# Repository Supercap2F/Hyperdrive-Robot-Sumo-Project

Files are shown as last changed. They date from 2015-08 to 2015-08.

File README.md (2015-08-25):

# Hyperdrive-Robot-Sumo-Project
Open Source Robot Sumo Project

* Start Date: Friday, November 28, 2014
*  End Date: ---
*   Version: 1.0

# About
The project started out on November 28th, 2014 - But under a different name: "Epsilon - The Universal Robot".
After more work was done, it was changed to "Hyperdrive!", named after my one of my favorite songs from the band
Guardian. The robot's main function is for Robot sumo, but will also have programs that will allow it to also
be a line flowing robot, and more.

#### Note: You can find photos of the robot in: Hyperdrive-Robot-Sumo-Project/Images/Robot Photos

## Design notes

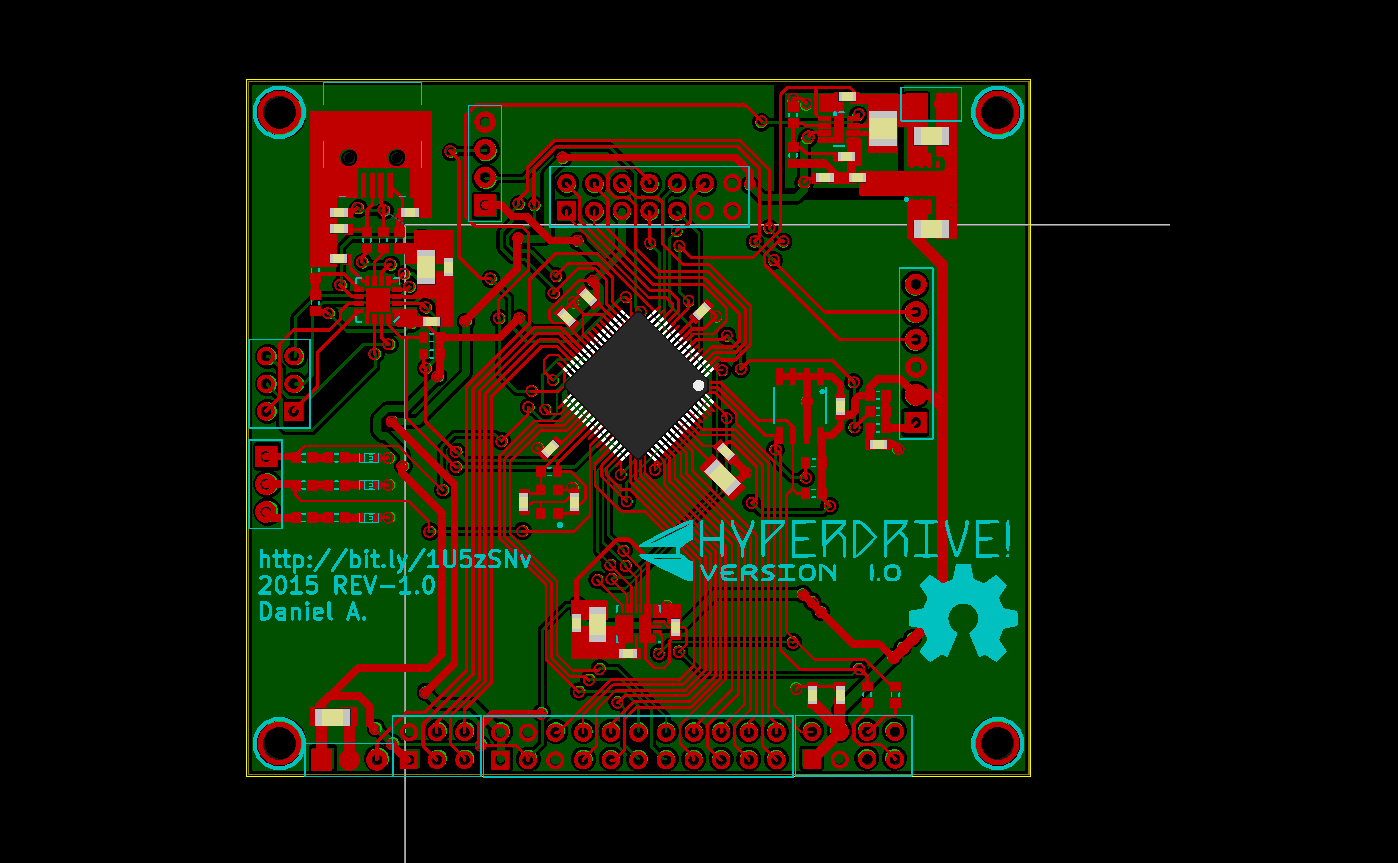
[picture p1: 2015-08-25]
Images/Robot Photos/Hyperdrive_Main_PCB.png

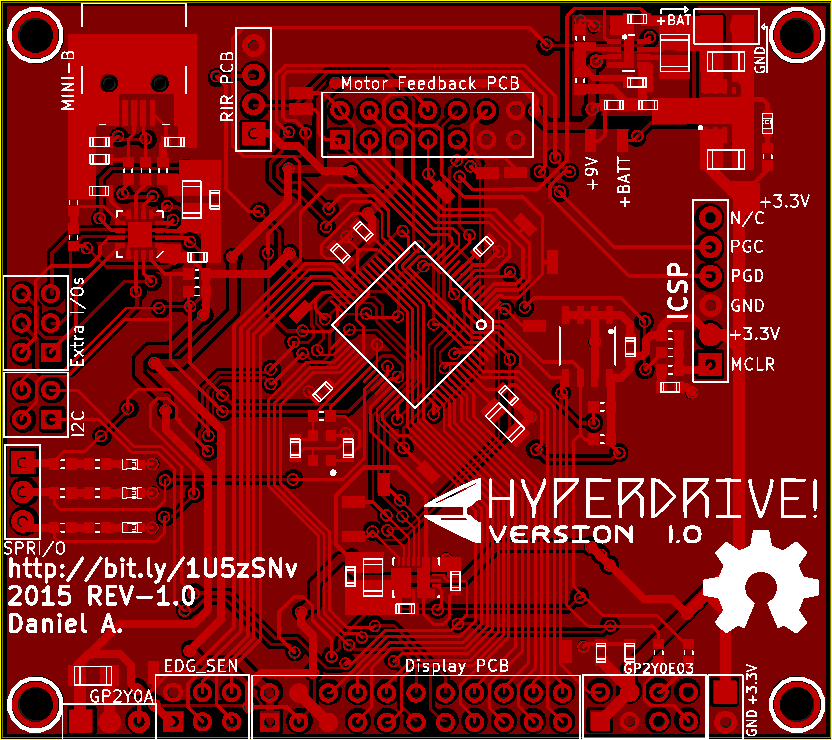
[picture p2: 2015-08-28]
Images/Robot Photos/Hyperdrive_Main_PCB#2.JPG

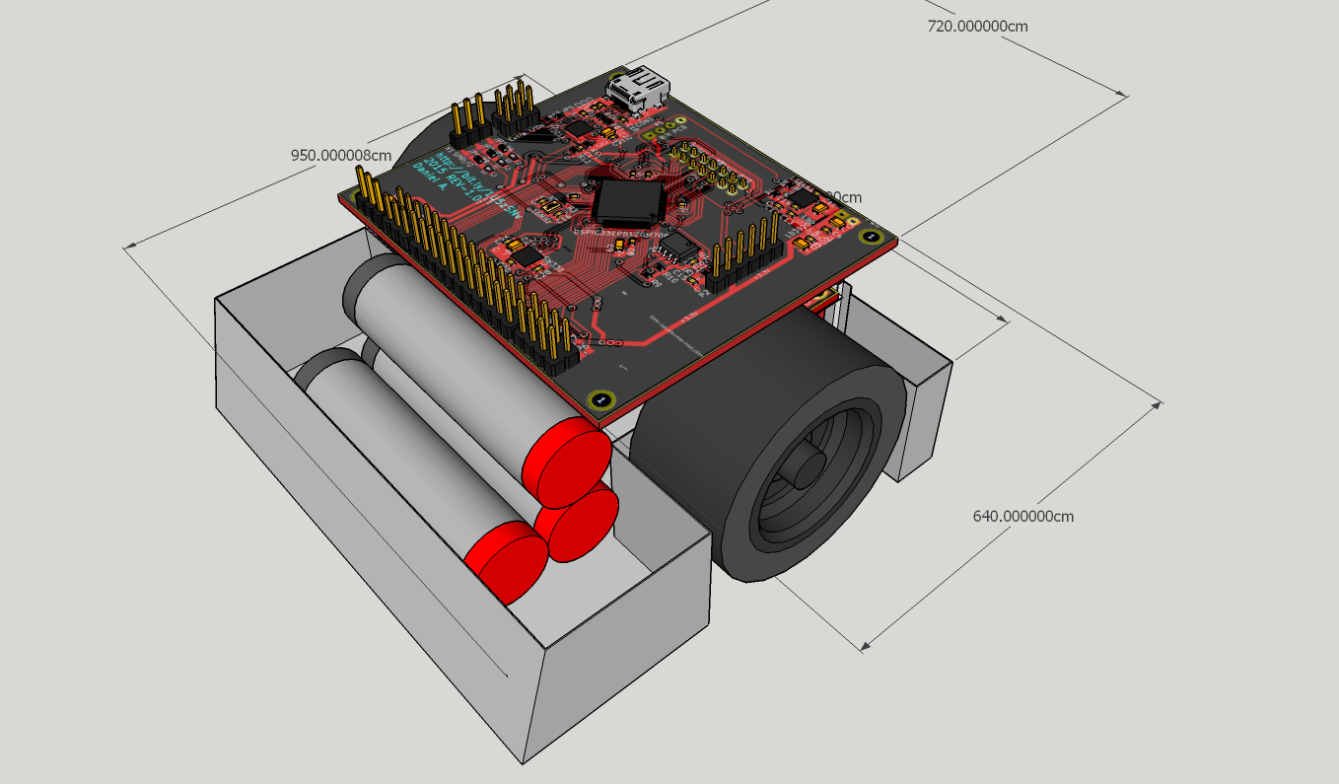
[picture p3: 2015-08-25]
Images/Robot Photos/Hyperdrive_3D_Model_#1.png

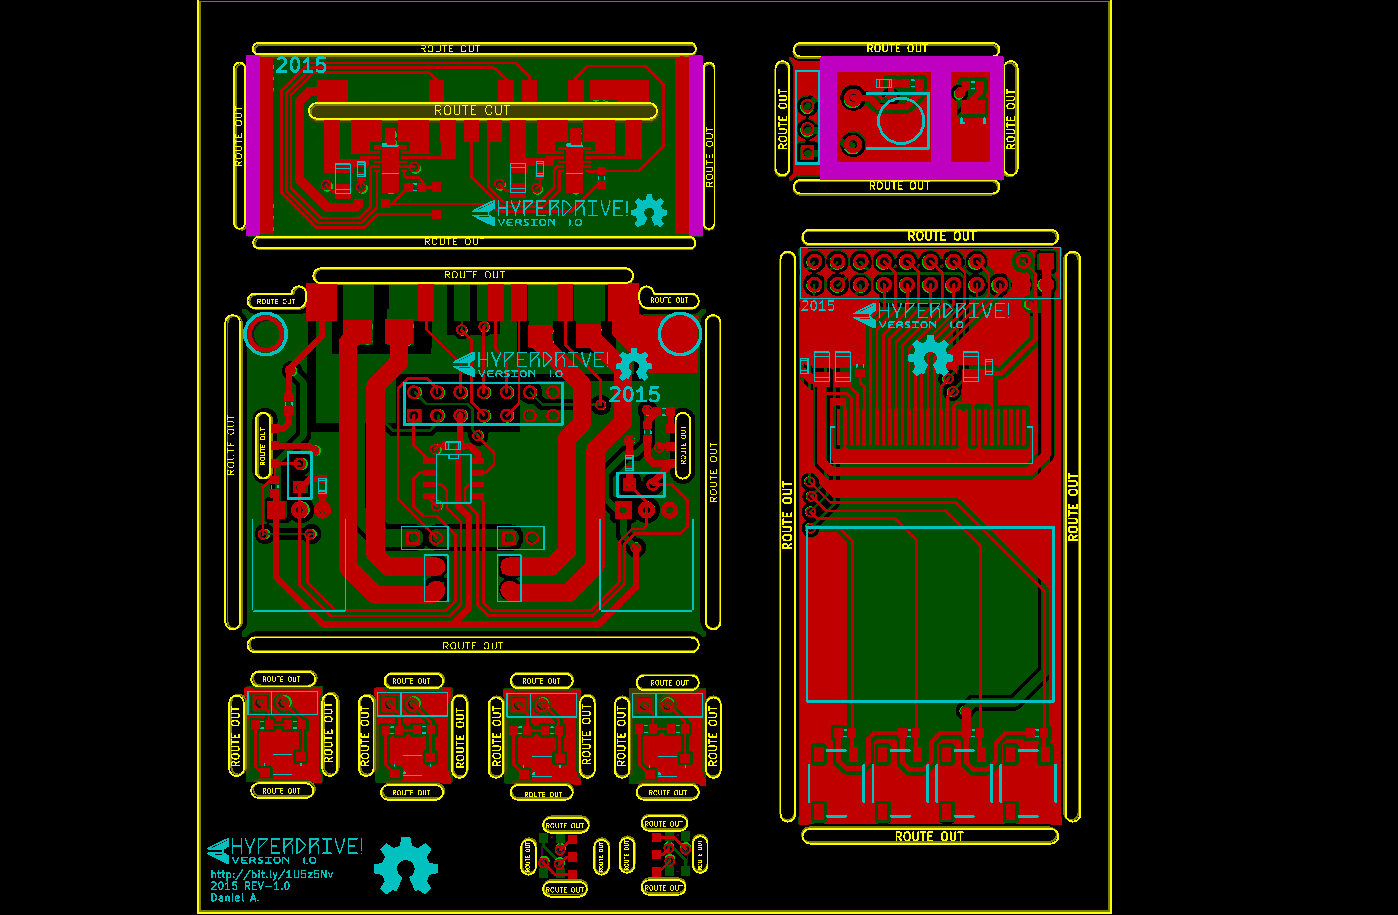
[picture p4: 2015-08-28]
Images/Robot Photos/Hyperdrive!_Odd_PCB_Photo.png

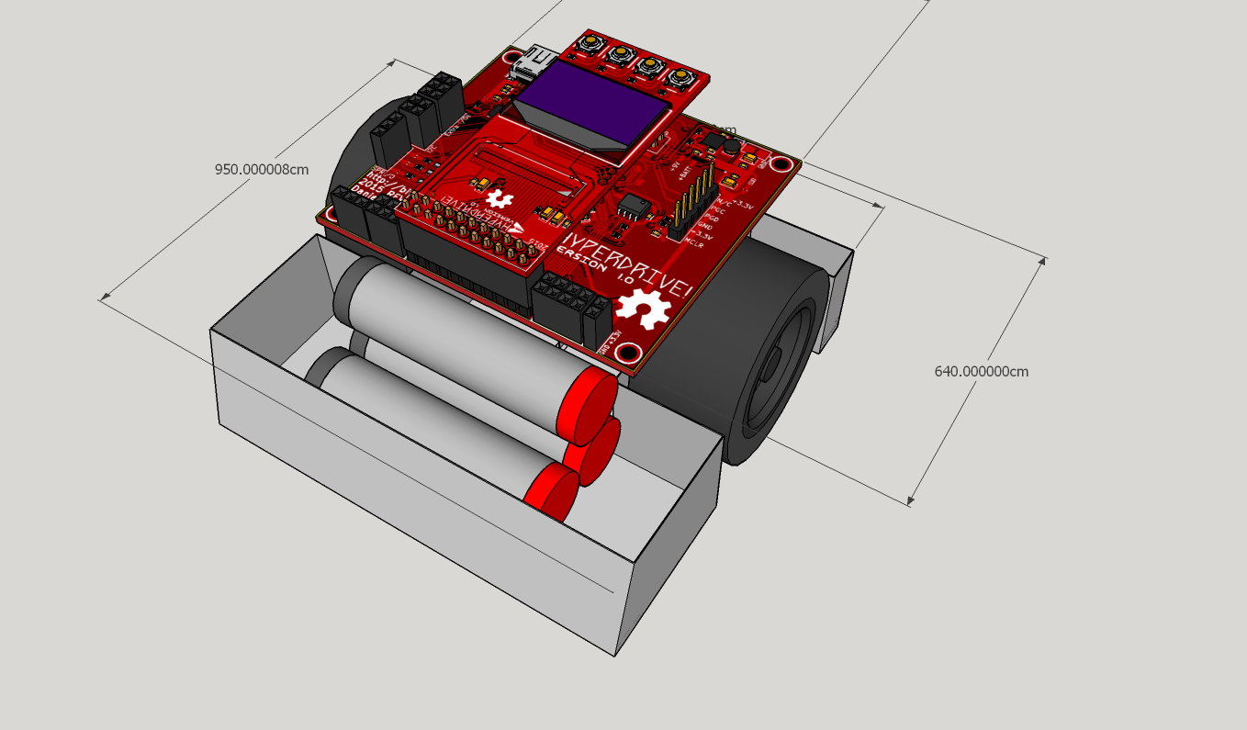
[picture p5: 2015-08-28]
Images/Robot Photos/Hyperdrive_3D_Model_#3.png

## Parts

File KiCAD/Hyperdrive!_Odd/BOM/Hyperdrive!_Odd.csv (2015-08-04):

ref | value | footprint | Type | Price | Digikey Part No.
C1 | 10u | ~ | Tan
C2 | 1u | ~ | Ceramic
C3 | 10u | ~ | Tan
C4 | 1u | ~ | Ceramic
C5 | 0.1u | ~
C6 | 100n | ~
C7 | 100n | ~
C8 | 100n | ~
C9 | 2.2u | ~
C10 | 4.7u | ~
C11 | 2.2u | ~
C12 | 100n | ~
K1 | ES1
K2 | ES2
K3 | ES3
K4 | ES4
LCD1 | 128X64_LCD | ~
P1 | CONN_16
P2 | H-Bridge PCB
P3 | Main Processor PCB
P4 | MR
P5 | ML
P6 | CONN_22 | ~
R1 | 10K | ~
R2 | 160 | ~
R3 | 10K | ~
R4 | 160 | ~
R5 | 10K | ~
R6 | 160 | ~
R7 | 10K | ~
R8 | 160 | ~
R9 | 10K | ~
R10 | 10K | ~
R11 | 160 | ~
R12 | 10K | ~
R13 | 160 | ~
R14 | 10K | ~
R15 | 10K | ~
R16 | 10K | ~
R17 | 10K | ~
R18 | 10K | ~
R19 | 560K | ~
RV1 | 50K | ~
RV2 | 50K | ~
SW1 | SW_PUSH | ~
SW2 | SW_PUSH | ~
SW3 | SW_PUSH | ~
SW4 | SW_PUSH | ~
U1 | MAX14780
U2 | QRE1113 | ~
U3 | QRE1113 | ~
U4 | MAX14780
U5 | QRE1113 | ~
U6 | QRE1113 | ~
U7 | MCP6541 | ~
U8 | QRE1113 | ~
U9 | QRE1113 | ~

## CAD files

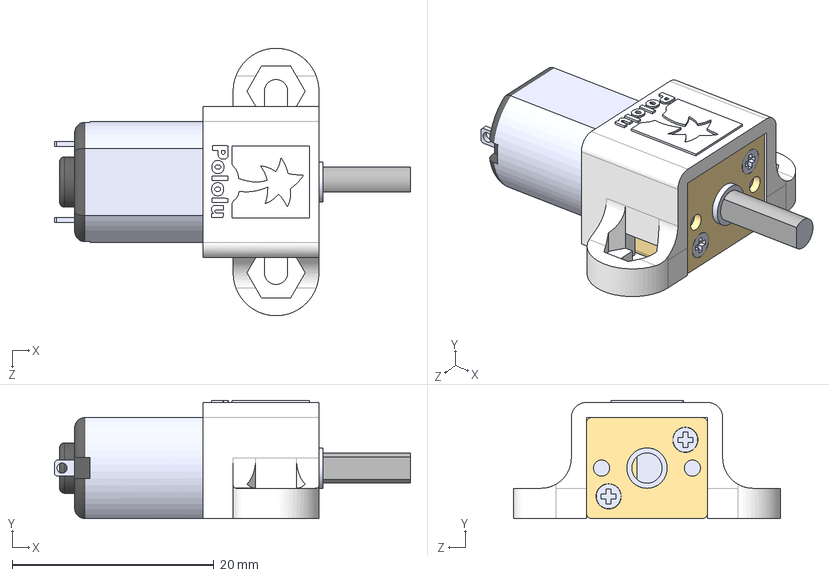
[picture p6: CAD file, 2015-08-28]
3D-Models/Components/micro-metal-gearmotor-with-1086-bracket.step
35.3 x 11.7 x 26.5 mm

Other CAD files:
3D-Models/Components/1200mAh_LiPoly.skp
3D-Models/Components/43.2x22_Wheel.skp
3D-Models/Components/Display.skp
3D-Models/Components/Display_PCB.skp
3D-Models/Components/Gull_Wing.skp
3D-Models/Components/Header_11x2.skp
3D-Models/Components/Header_2x1.skp
3D-Models/Components/Header_2x2.skp
3D-Models/Components/Header_3x1.skp
3D-Models/Components/Header_3x2.skp
3D-Models/Components/Header_4x2.skp
3D-Models/Components/Header_7x2.skp
3D-Models/Components/RB-POL-61-100x.skp

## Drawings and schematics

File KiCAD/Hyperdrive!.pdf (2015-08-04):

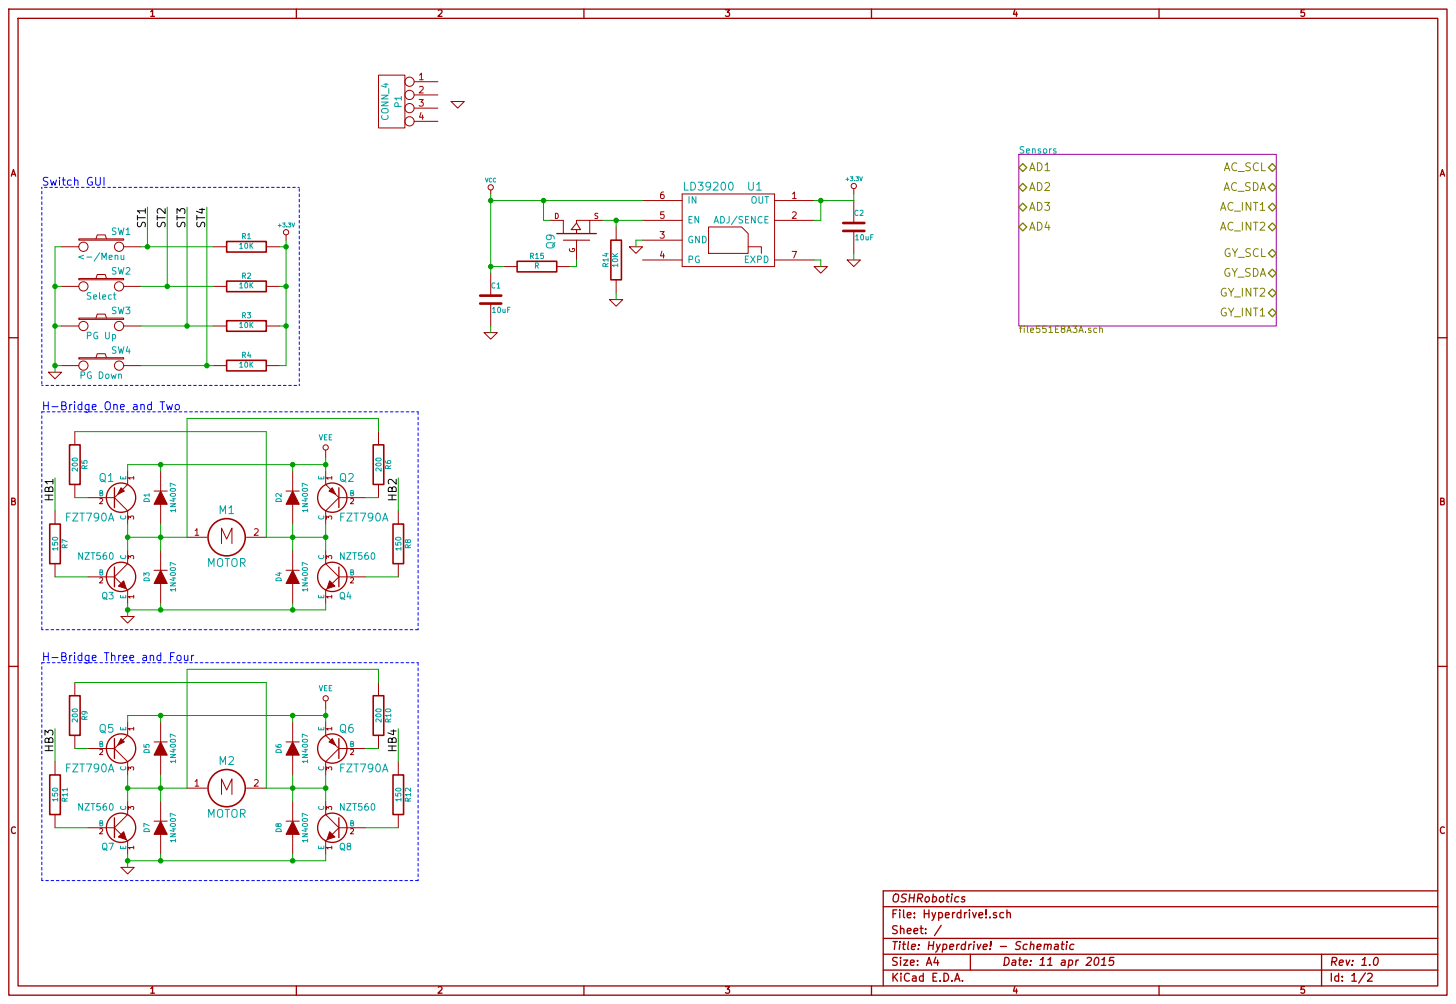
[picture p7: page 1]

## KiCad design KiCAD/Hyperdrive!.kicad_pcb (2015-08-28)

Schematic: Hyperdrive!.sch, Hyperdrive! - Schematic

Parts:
C1, C2, C6, C7, C8: 0.1u; Voltage 10-20V
C3, C4: 10uF
C5, C17, C18, C21, C23: 100n
C9: 10u; Voltage 16
C10, C14, C16: 20p
C11: 1u
C12: 0.47u
C13: 2.2u
C15: 0.1u
C19, C20: 47p
C22: 4.7u
CON1: USB-MINI-B
D1, D2, D3, D4: LED
FB1: 600R/1.3A
JP1: MCLR
JP2, JP3, JP4: JUMPER
JP5: RESET
K1: SPRI/O
L1: 47u
P1: RIR PCB
P2: ICSP
P3: Display PCB
P4: Motor Feedback PCB
P5: Extra I/Os
P7, P9: PWR
P8: I2C
R1, R13: 10K
R2: 100
R3: 1M
R4: 1908K
R5: 300K
R6, R7, R8: 220
R9, R10, R11, R12, R16: R
R14, R15: 27
TP1, TP2, TP3, TP4, TP5, TP6, TP7, TP8, TP9, TP10, TP11: TP
U1: 24AA256
U2: LD39200
U3: LT3464
U4: DSPIC33EP512GM706
U5: FT201X
X1: 16MHz

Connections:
+3.3V: C1.2, C2.1, C3.1, C5.1, C6.2, C7.1, C8.1, C17.1, P1.1, P2.2, P3.3, P4.5, P9.1, R1.2, R9.1, R10.1, R11.1, R12.1, R13.1, R16.1, TP2.1, U1.8 (Vcc), U2.1 (OUT), U2.2 (OUT), U2.3 (ADJ/SENCE), U4.10 (VDD), U4.19 (AVDD), U4.26 (VDD), U4.38 (VDD), U4.57 (VDD), U5.1 (VCCIO); also elsewhere on the board
+9V: C12.1, P3.1, P3.2, TP3.1, U3.3 (OUT)
+BATT: C4.1, C11.1, L1.2, P7.1, TP1.1, U2.6 (EN), U2.7 (IN), U2.8 (IN), U3.1 (CTRL), U3.7 (Vin), U4.12 (AN9/RPI27/RA11)
/CS#: P3.17, U4.52 (RP56/PWM5H/PMWR/RC8)
/D0: P3.9, U4.21 (OA3OUT/AN6/C3IN4-/C4IN1+/RP48/OCFB/RC0)
/D1: P3.10, U4.22 (OA3IN-/AN7/C3IN1-/C4IN1-/RP49/RC1)
/D2: P3.11, U4.23 (OA3IN+/AN8/C3IN3-/C3IN1+/RPI50/U1RTS/BC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)
/D3: P3.12, U4.35 (AN29/SCK1/RPI51/RC3)
/D4: P3.13, U4.36 (AN30/SDA1/RPI52/RC4)
/D5: P3.14, U4.37 (AN31/SCL1/RPI53/RC5)
/D6: P3.15, U4.50 (RP54/PWM6H/RC6)
/D7: P3.16, U4.51 (RP55/PWM6L/PMBE/RC7)
/D/C#: P3.6, U4.45 (AN48/CVREF2O/RPI58/PMCS1/RC10)
/DIRL: P4.7, TP7.1, U4.48 (TCK/AN26/CVREF1O/SOSCO/RP40/T4CK/RB8)
/DIRR: P4.10, TP10.1, U4.46 (OA5OUT/AN25/C5IN4-/RP39/INT0/RB7)
/E/RD#: P3.8, U4.47 (SOSCI/RPI61/RC13)
/FAULTL: P4.12, TP11.1, U4.60 (RP42/PWM3H/PMD0/RB10)
/FAULTR: P4.9, TP9.1, U4.49 (TMS/OA5IN-/AN27/C5IN4-/RP41/RB9)
/I/O1: JP2.2, K1.1, U4.11 (AN10/RPI28/RA12)
/I/O2: JP3.2, K1.2 (PM), U4.42 (RPI72/RD8)
/IRBDS: P1.2, U4.63 (RPI45/PWM2L/CTPLS/PMD3/RB13)
/IRPWM: P1.3, U4.62 (RPI44/PWM2H/PMD2/RB12)
/MCLR: JP1.2, P2.1, R1.1, R2.1
/MSL: P4.1, TP4.1, U4.14 (OA2IN+/AN1/C2IN1+/RPI17/RA1)
/MSR: P4.2, TP5.1, U4.13 (OA2OUT/AN0/C2IN4-/C4IN3-/RPI16/RA0)
/PGC: P2.5, U4.17 (PGEC1/OA1IN+/AN4/C1IN3-/C1IN1+/C2IN3-/R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)
/PGD: P2.4, U4.18 (PGED1/OA1IN-/AN5/C1IN1-/(CTMUC)/RP35/RT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)
/PWML: P4.8, TP8.1, U4.3 (RPI47/PWM1L/T5CK/T6CK/PMD7/RB15)
/PWMR: P4.6, TP6.1, U4.2 (RPI46/PWM1H/T3CK/T7CK/PMD6/RB14)
/R/W#: P3.7, U4.24 (AN11/C1IN2-/U1CTS/FLT4/PMA12/RC11)
/RES#: P3.20, U4.55 (RP57/PWM5L/RC9)
/SCL/FM+: P8.3, R11.2, U4.43 (PGED2/ASDA2/RP37/RB5), U5.16 (SCL)
/SDA/FM+: P8.4, R12.2, U4.44 (PGEC2/ASCL2/RP38/PMCS2/RB6), U5.2 (SDA)
/SHDN: U3.8 (SHDN), U4.32 (FLT32/SCL2/RP36/PMA8/RB4)
/ST1: P3.21, U4.58 (RPI96/RF0)
/ST2: P3.22, U4.59 (RP97/RF1)
/ST3: P3.19, U4.54 (RP70/RD6)
/ST4: P3.18, U4.53 (RP69/PMRD/RD5)
/Sensors /AD1: U4.27 (AN12/C2IN2-/C5IN2-/U2RTS/BCLK2/FLT5/PMA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); also elsewhere on the board
/Sensors /AD2: U4.28 (AN13/C3IN2-/U2CTS/FLT6/PMA10/RE13); also elsewhere on the board
/Sensors /AD3: U4.29 (AN14/RPI94/FLT7/PMA1/RE14); also elsewhere on the board
/Sensors /AD4: U4.30 (AN15/RPI95/FLT8/PMA0/RE15); also elsewhere on the board
/Sensors /IMU_DEN_G: U4.64 (TDO/PWM4H/PMD4/RA10); also elsewhere on the board
/Sensors /IMU_INT1_A: U4.33 (OA5IN+/AN24/C5IN3-/C5IN1+/SDO1/RP20/T1C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); also elsewhere on the board
/Sensors /IMU_INT1_G: U4.31 (SDA2/RPI24/PMA9/RA8); also elsewhere on the board
/Sensors /IMU_INT2_A: U4.1 (TDI/PWM4L/PMD5/RA7); also elsewhere on the board
/Sensors /IMU_INT2_G: U4.34 (AN28/SDI1/RPI25/RA9); also elsewhere on the board
/Sensors /IMU_SCL: P8.1, R9.2, U1.6 (SCL), U4.5 (AN18/ASCL1/RPI119/PMA4/RG7); also elsewhere on the board
/Sensors /IMU_SDA: P8.2, R10.2, U1.5 (SDA), U4.6 (AN17/ASDA1/RP120/PMA3/RG8); also elsewhere on the board
/Sensors /IRDS_VO: U4.16 (PGEC3/VREF+/CVREF+/OA1OUT/AN3/C1IN4-/C4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); also elsewhere on the board
/Sensors /IRLDS_VO: U4.15 (PGED3/VREF-/OA2IN-/AN2/C2IN1-/SS1/RPI32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); also elsewhere on the board
/VBUS: C21.1, C22.1, FB1.2, U5.10 (VCC)
/VDD: P4.3, U4.8 (AN16/RPI121/PMA2/RG9)
/VDD2: P4.4, U4.4 (AN19/RP118/PMA5/RG6)
GND: C1.1, C2.2, C3.2, C4.2, C5.2, C6.1, C7.2, C8.2, C9.2, C10.2, C11.2, C13.2, C15.2, C16.2, C17.2, C18.2, C19.2, C20.2, C21.2, C22.2, C23.2, CON1.5 (GND), CON1.6 (SHELL1), CON1.7 (SHELL2), CON1.8 (SHELL3), CON1.9 (SHELL4), D1.2 (K), D2.2 (K), D3.2 (K), D4.2 (K), JP5.2, P1.4, P2.3, P3.4, P3.5, P4.11, P4.13, P4.14, P7.2 (PM), P9.2 (PM), R5.2, U1.1 (A0), U1.2 (A1), U1.3 (A2), U1.4 (Vss), U1.7 (WP), U2.4 (GND), U2.9 (EXPD), U3.4 (GND), U4.9 (VSS), U4.20 (AVSS), U4.25 (VSS), U4.41 (VSS), U5.3 (GND), U5.13 (GND), U5.17 (GND), X1.3, X1.4; also elsewhere on the board
unnamed: C18.1, CON1.1 (VBUS), FB1.1
unnamed: C19.1, CON1.2 (D-), R14.1
unnamed: C20.1, CON1.3 (D+), R15.1
unnamed: C15.1, JP1.1
unnamed: JP5.1, R13.2, U5.9 (RESET)
unnamed: C9.1, U4.56 (VCAP)
unnamed: C23.1, U5.8 (3V3OUT)
unnamed: R14.2, U5.7 (USBDM)
unnamed: R15.2, U5.6 (USBDP)
unnamed: JP3.1, R7.1
unnamed: JP4.1, R8.1
unnamed: P5.1, U5.12 (CBUS0)
unnamed: P5.2, U5.11 (CBUS1)
unnamed: P5.3, U5.5 (CBUS2)
unnamed: P5.4, U5.14 (CBUS3)
unnamed: P5.5, U5.4 (CBUS4)
unnamed: P5.6, U5.15 (CBUS5)
unnamed: D1.1 (A), R6.2
unnamed: D2.1 (A), R7.2
unnamed: D3.1 (A), R8.2
unnamed: JP2.1, R6.1
unnamed: R2.2, U4.7 (MCLR)
unnamed: C16.1, R3.2, U4.40 (OSC2/CLKO/RPI63/RC15), X1.1
unnamed: C10.1, R3.1, U4.39 (AN49/OSC1/CLKI/RPI60/RC12), X1.2
unnamed: D4.1 (A), R16.2
unnamed: C12.2, C13.1, C14.1, R4.1, U3.5 (CAP)
unnamed: C14.2, R4.2, R5.1, U3.2 (FB)
unnamed: L1.1, U3.6 (SW)

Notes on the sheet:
Place ISCP jack as close as possible to the Microcontroller
ICSP Jack
PLLDIV=33 PLLPOST=0 PLLPRE=0
3.3V Regulator
FT201X USB to I2C Bridge
400KHz I2C Pull-ups FM
1MHz I2C Pull-ups FM+
LCD Boost Converter
This conector goes to the PCB with the display and control switches. See the hyperdrive project folder for schematics/PCB layouts
The conector goes to the PCB with the motor feedback sensors. See the hyperdrive project folder for schematics/PCB layouts.
The conector goes to the PCB with the rear IR sensors on it. See the Hyperdrive! project folder for schematics/ PCB layouts.
256Kbit EEPROM
Spare I/Os - Status LEDs
Main Processor
PWR LED
Extra Connectors

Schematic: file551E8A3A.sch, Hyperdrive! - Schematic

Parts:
C24, C27: 10u
C25, C26, C28, C29: 100n
C30: 10n; Voltage 25V
JP6: SCL
JP7: SDA
P6: EDG_SEN
TP12, TP13, TP14, TP15, TP16, TP17, TP18: TP
U6: GP2Y0A51SK0F
U7: LSM330
U8: GP2Y0E03

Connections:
+3.3V: C24.1, C25.1, C26.1, C27.1, C28.1, C29.1, P6.1, U6.1 (Vcc), U7.1 (VDD_IO), U7.3 (VDD_IO), U7.7 (CS_G), U7.8 (CS_A), U7.22 (VDD), U7.23 (VDD), U7.24 (VDD), U8.1 (VDD), U8.4 (VIN_I/O); also elsewhere on the board
/Sensors /AD1: P6.3; also elsewhere on the board
/Sensors /AD2: P6.4; also elsewhere on the board
/Sensors /AD3: P6.5; also elsewhere on the board
/Sensors /AD4: P6.6; also elsewhere on the board
/Sensors /IMU_DEN_G: TP18.1, U7.13 (DEN_G); also elsewhere on the board
/Sensors /IMU_INT1_A: TP14.1, U7.11 (INT1_A); also elsewhere on the board
/Sensors /IMU_INT1_G: TP16.1, U7.10 (INT1_G); also elsewhere on the board
/Sensors /IMU_INT2_A: TP15.1, U7.12 (INT2_A); also elsewhere on the board
/Sensors /IMU_INT2_G: TP17.1, U7.9 (DRDY_G/INT2_G); also elsewhere on the board
/Sensors /IMU_SCL: JP6.2, U7.2 (SCL_A/G); also elsewhere on the board
/Sensors /IMU_SDA: JP7.2, U7.4 (SDA/SDI_A/G); also elsewhere on the board
/Sensors /IRDS_VO: TP12.1, U6.3 (VO); also elsewhere on the board
/Sensors /IRLDS_VO: TP13.1, U8.2 (Vout); also elsewhere on the board
GND: C24.2, C25.2, C26.2, C27.2, C28.2, C29.2, C30.2, P6.2, U6.2 (GND), U7.5 (SDO_G), U7.6 (SDO_A), U7.14 (RES), U7.15 (RES), U7.16 (RES), U7.17 (RES), U7.18 (RES), U7.19 (GND), U7.20 (GND), U8.3 (GND); also elsewhere on the board
unnamed: JP6.1, U8.6 (SCL)
unnamed: JP7.1, U8.7 (SDA)
unnamed: C30.1, U7.21 (CAP)

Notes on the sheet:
There are four edge sensors in total. Each one is mounted on a seperate PCB on each corner of the robot. The schematic of the sensors can be found at: C:\Users\OPTIPLEX 960\Documents \Electronics\Robots\Hyperdrive!
Edge Sensors
4-50cm IR Distance Sensor
2-15cm IR Distance Sensor
IMU - Gyroscope/Accelerometer

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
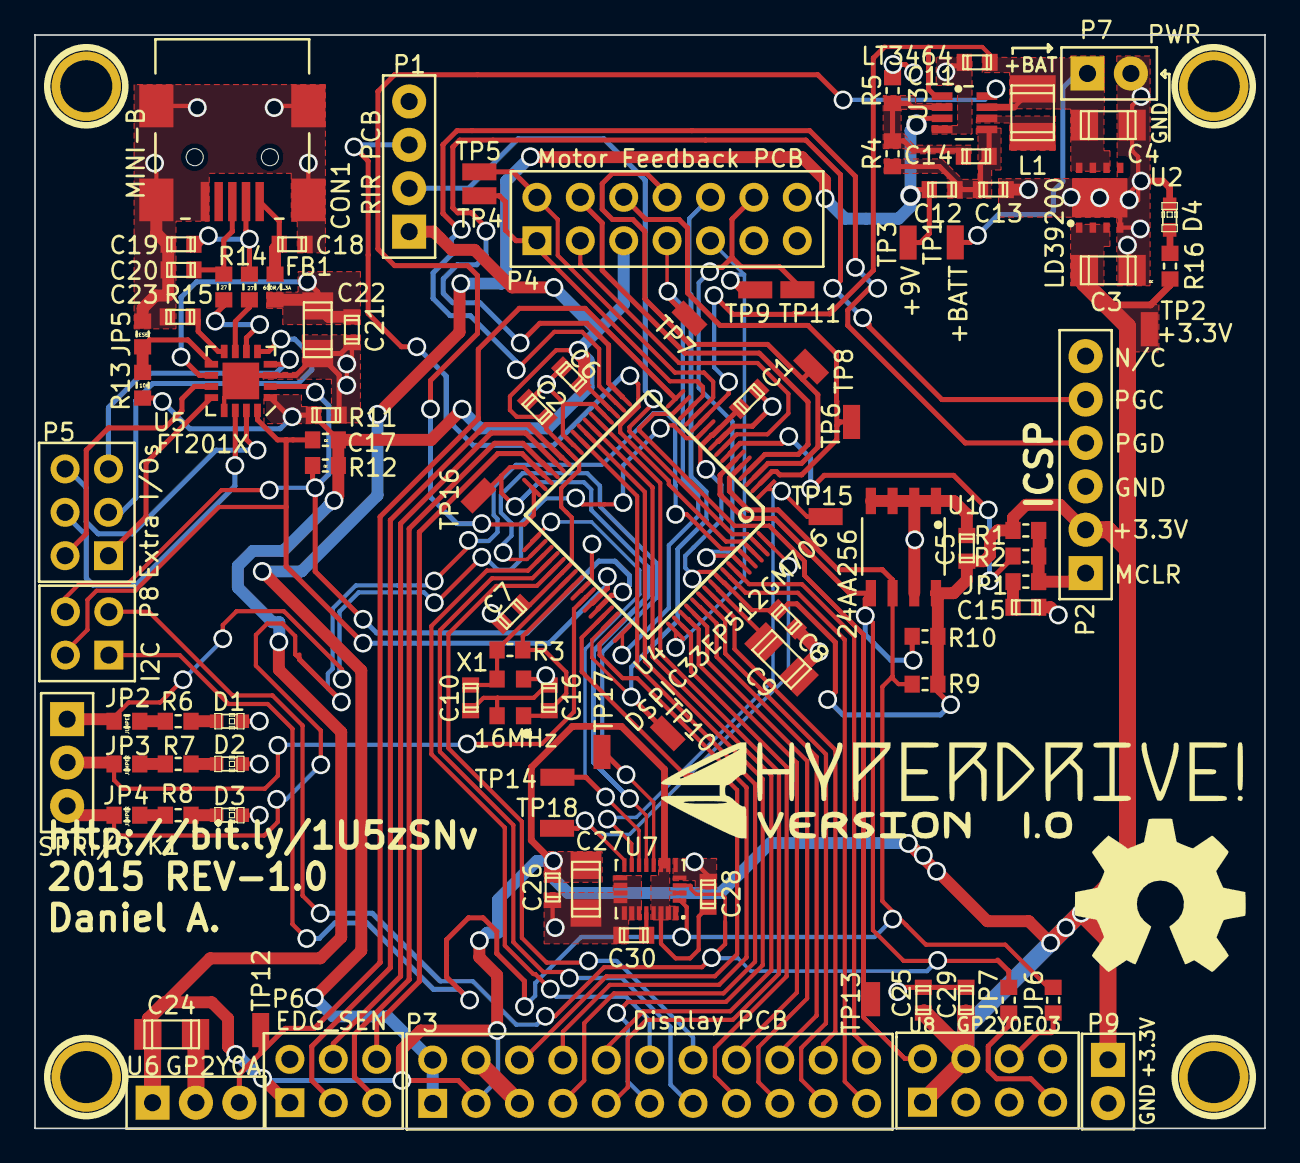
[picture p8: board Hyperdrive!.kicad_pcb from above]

Board: 2 copper layers, 72.0 x 64.0 mm, 98 parts (0 on the bottom side), 87 nets.

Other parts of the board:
VAL: REF; Hyperdrive!_F.SilkS_40mm

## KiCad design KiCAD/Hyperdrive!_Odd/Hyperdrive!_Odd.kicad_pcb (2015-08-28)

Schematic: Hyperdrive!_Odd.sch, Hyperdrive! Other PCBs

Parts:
B1, B2: LiPoly
C1, C3: 10u
C2, C4: 1u
C5: 0.1u
C6, C7, C8, C12, C13: 100n
C9, C11: 2.2u
C10: 4.7u
D1: IR
K1: ES1
K2: ES2
K3: ES3
K4: ES4
LCD1: 128X64_LCD
P1, P2: H-Bridge PCB
P3: Main Processor PCB
P4: MR
P5: ML
P6: Display PCB
P7: RIR PCB
R1, R3, R5, R7, R9, R10, R12, R14, R15, R16, R17, R18: 10K
R2, R4, R6, R8, R11, R13: 160
R19: 560K
R20: 100
R21: 165
RV1, RV2: 50K
SW1, SW2, SW3, SW4: SW_PUSH
U1, U4: MAX14780
U2, U3, U5, U6, U8, U9: QRE1113
U7: MCP6541
U10: TSOP4038

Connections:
3V3: C5.1, P2.5, P3.5, R11.1, R12.1, R13.1, R14.1, RV1.1, RV2.1, U7.8
+3.3V: P1.5, R1.1, R10.1; also elsewhere on the board
+3.3VB: C8.1, C9.1, LCD1.6 (VBAT), LCD1.9 (VDD), LCD1.12 (BS2), P6.3, R15.2, R16.2, R17.2, R18.2
+3.3VC: C13.1, P7.3, R20.1
/CS#: LCD1.13 (CS#), P6.17
/D0: LCD1.18 (D0), P6.9
/D1: LCD1.19 (D1), P6.10
/D2: LCD1.20 (D2), P6.11
/D3: LCD1.21 (D3), P6.12
/D4: LCD1.22 (D4), P6.13
/D5: LCD1.23 (D5), P6.14
/D6: LCD1.24 (D6), P6.15
/D7: LCD1.25 (D7), P6.16
/D/C#: LCD1.15 (D/C#), P6.6
/DIRL: P1.9, U1.6 (DIR)
/DIRLA: P2.9, P3.7
/DIRR: P1.7, U4.6 (DIR)
/DIRRA: P2.7, P3.10
/E/RD#: LCD1.17 (E/RD#), P6.8
/FAULTL: P1.11, R1.2, U1.7 (FAULT)
/FAULTLA: P2.11, P3.12
/FAULTR: P1.8, R10.2, U4.7 (FAULT); also elsewhere on the board
/FAULTRA: P2.8, P3.9
/IRBDS: P7.2, U10.1 (Out)
/IRPWM: P7.1, R21.2
/M1L: P1.15, U1.2 (M1)
/M1LA: P2.15, P5.1
/M1R: P1.13, U4.2 (M1)
/M1RA: P2.13, P4.1
/M2L: P1.16, U1.11 (M2)
/M2LA: P2.16, P5.2 (PM)
/M2R: P1.14, U4.11 (M2)
/M2RA: P2.14, P4.2 (PM)
/MSLA: P3.1, U7.1
/MSRA: P3.2, U7.7
/PWML: P1.10, U1.5 (PWM)
/PWMLA: P2.10, P3.8
/PWMR: P1.6, U4.5 (PWM)
/PWMRA: P2.6, P3.6
/R/W#: LCD1.16 (R/W#), P6.7
/RES#: LCD1.14 (RES#), P6.20
/ST1: P6.21, R15.1, SW1.2
/ST2: P6.22, R16.1, SW2.2
/ST3: P6.19, R17.1, SW3.2
/ST4: P6.18, R18.1, SW4.2
/VDDA: B1.1, P2.1, P2.2, P2.3, P2.4, P3.3
/VDDA2: B1.2, B2.1, P3.4
GND: C1.2, C2.2, C3.2, C4.2, P1.12, U1.1 (COM), U1.4 (SNS), U1.8 (EN), U1.9 (GND), U1.12 (COM), U1.15 (EP), U4.1 (COM), U4.4 (SNS), U4.8 (EN), U4.9 (GND), U4.12 (COM), U4.15 (EP)
GNDA: B2.2, C5.2, C6.2, C7.2, P2.12, P3.11, P3.13, P3.14, RV1.3, RV2.3, U7.4, U8.2 (Cathode), U8.4 (Emitter), U9.2 (Cathode), U9.4 (Emitter)
GNDB: C8.2, C9.2, C10.2, C11.2, C12.2, LCD1.8 (VSS), LCD1.10 (BS0), LCD1.11 (BS1), LCD1.29 (VLSS), P6.4, P6.5, R19.2, SW1.1, SW2.1, SW3.1, SW4.1
GNDC: C13.2, D1.1 (A), P7.4, U10.2 (GND)
unnamed: R13.2, U9.1 (Anode_)
unnamed 52: R14.2, U7.6, U9.3 (Collector); also elsewhere on the board
unnamed: R11.2, U8.1 (Anode_)
unnamed 54: R12.2, U7.2, U8.3 (Collector); also elsewhere on the board
unnamed: K1.2 (PM), R3.2, U2.3 (Collector)
unnamed: K3.1, R6.1, R7.1
unnamed: R6.2, U5.1 (Anode_)
unnamed: K3.3, U5.2 (Cathode), U5.4 (Emitter)
unnamed: K3.2 (PM), R7.2, U5.3 (Collector)
unnamed: K1.1, R2.1, R3.1
unnamed: R2.2, U2.1 (Anode_)
unnamed: K1.3, U2.2 (Cathode), U2.4 (Emitter)
unnamed: K4.3, U6.2 (Cathode), U6.4 (Emitter)
unnamed: K4.2 (PM), R9.2, U6.3 (Collector)
unnamed: K2.1, R4.1, R5.1
unnamed: R4.2, U3.1 (Anode_)
unnamed: K2.3, U3.2 (Cathode), U3.4 (Emitter)
unnamed: K2.2 (PM), R5.2, U3.3 (Collector)
unnamed: K4.1, R8.1, R9.1
unnamed: R8.2, U6.1 (Anode_)
unnamed: D1.2 (K), R21.1
unnamed 72: C7.1, RV2.2, U7.5; also elsewhere on the board
unnamed 73: C6.1, RV1.2, U7.3; also elsewhere on the board
unnamed: R20.2, U10.3 (Vcc)
unnamed: LCD1.26 (IREF), R19.1
unnamed: C10.1, LCD1.27 (VCOMH)
VCC: C11.1, C12.1, LCD1.28 (VCC), P6.1, P6.2
VDD: C1.1, C2.1, C3.1, C4.1, P1.1, P1.2, P1.3, P1.4, U1.3 (Vdd), U1.10 (Vdd), U4.3 (Vdd), U4.10 (Vdd)

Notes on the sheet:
Vcc
Out
GND
Edge Sensor One PCB
Edge Sensor Three PCB
Edge Sensor Two PCB
Edge Sensor Four PCB
Dual H-Bridge PCB
Motor FeedBack PCB
Display/GUI PCB
Rear IR Sensor PCB
Battery input

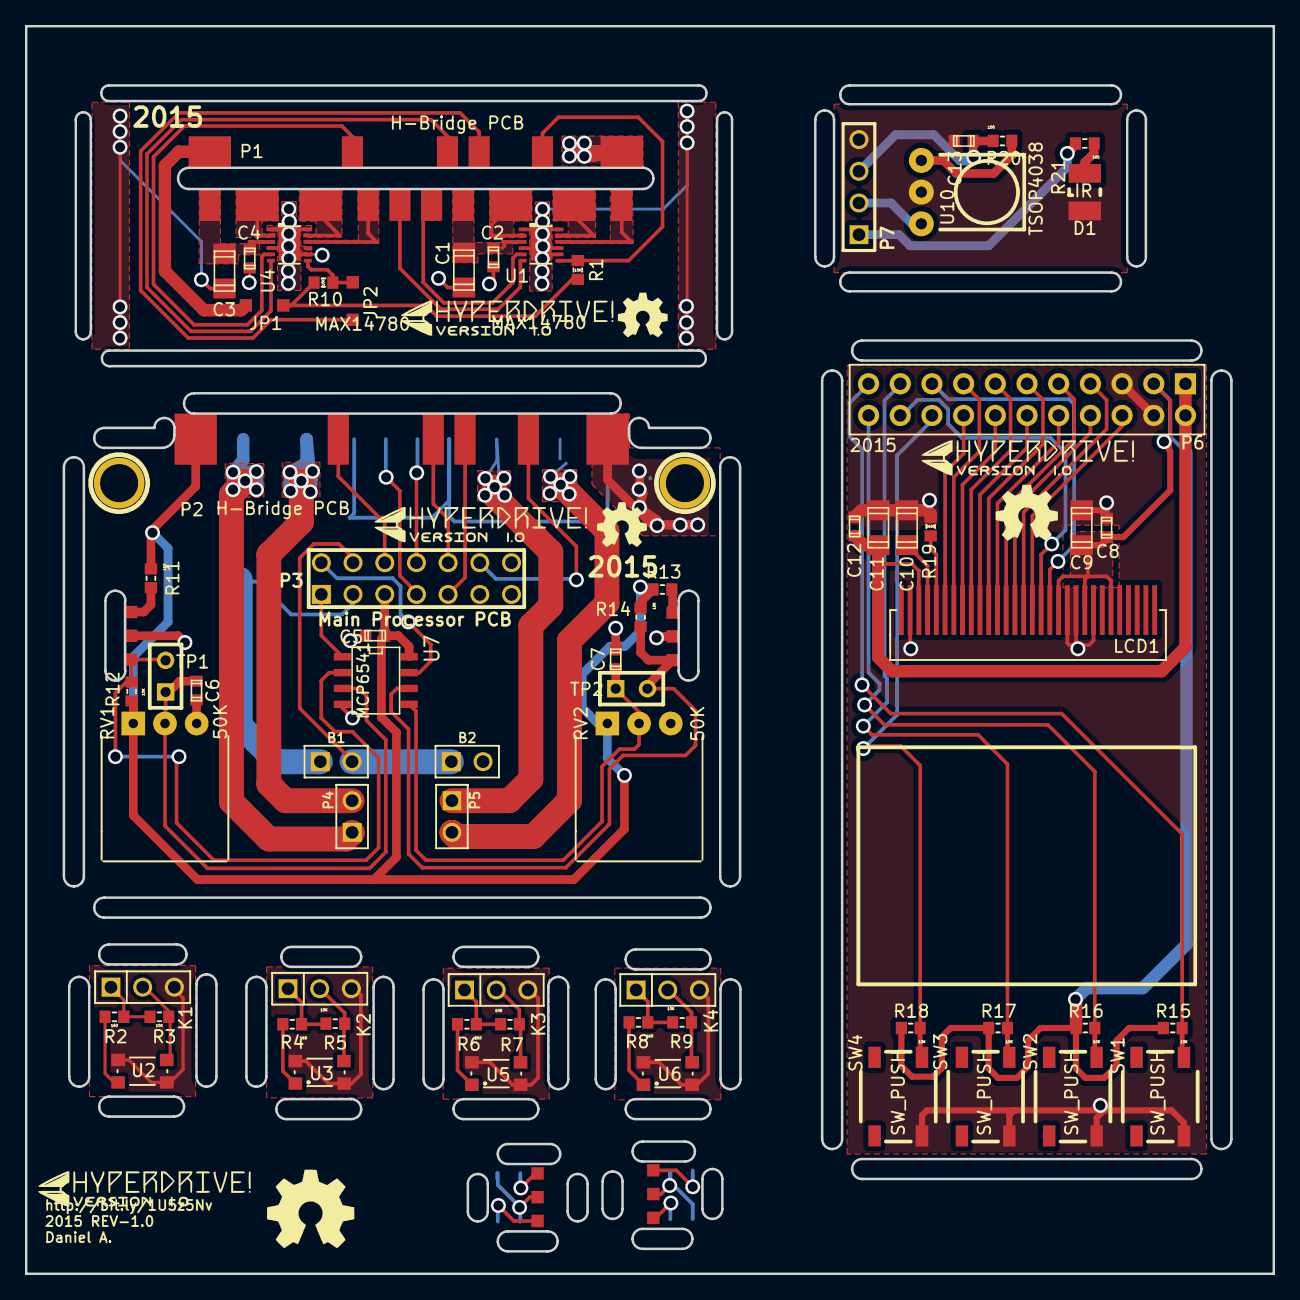
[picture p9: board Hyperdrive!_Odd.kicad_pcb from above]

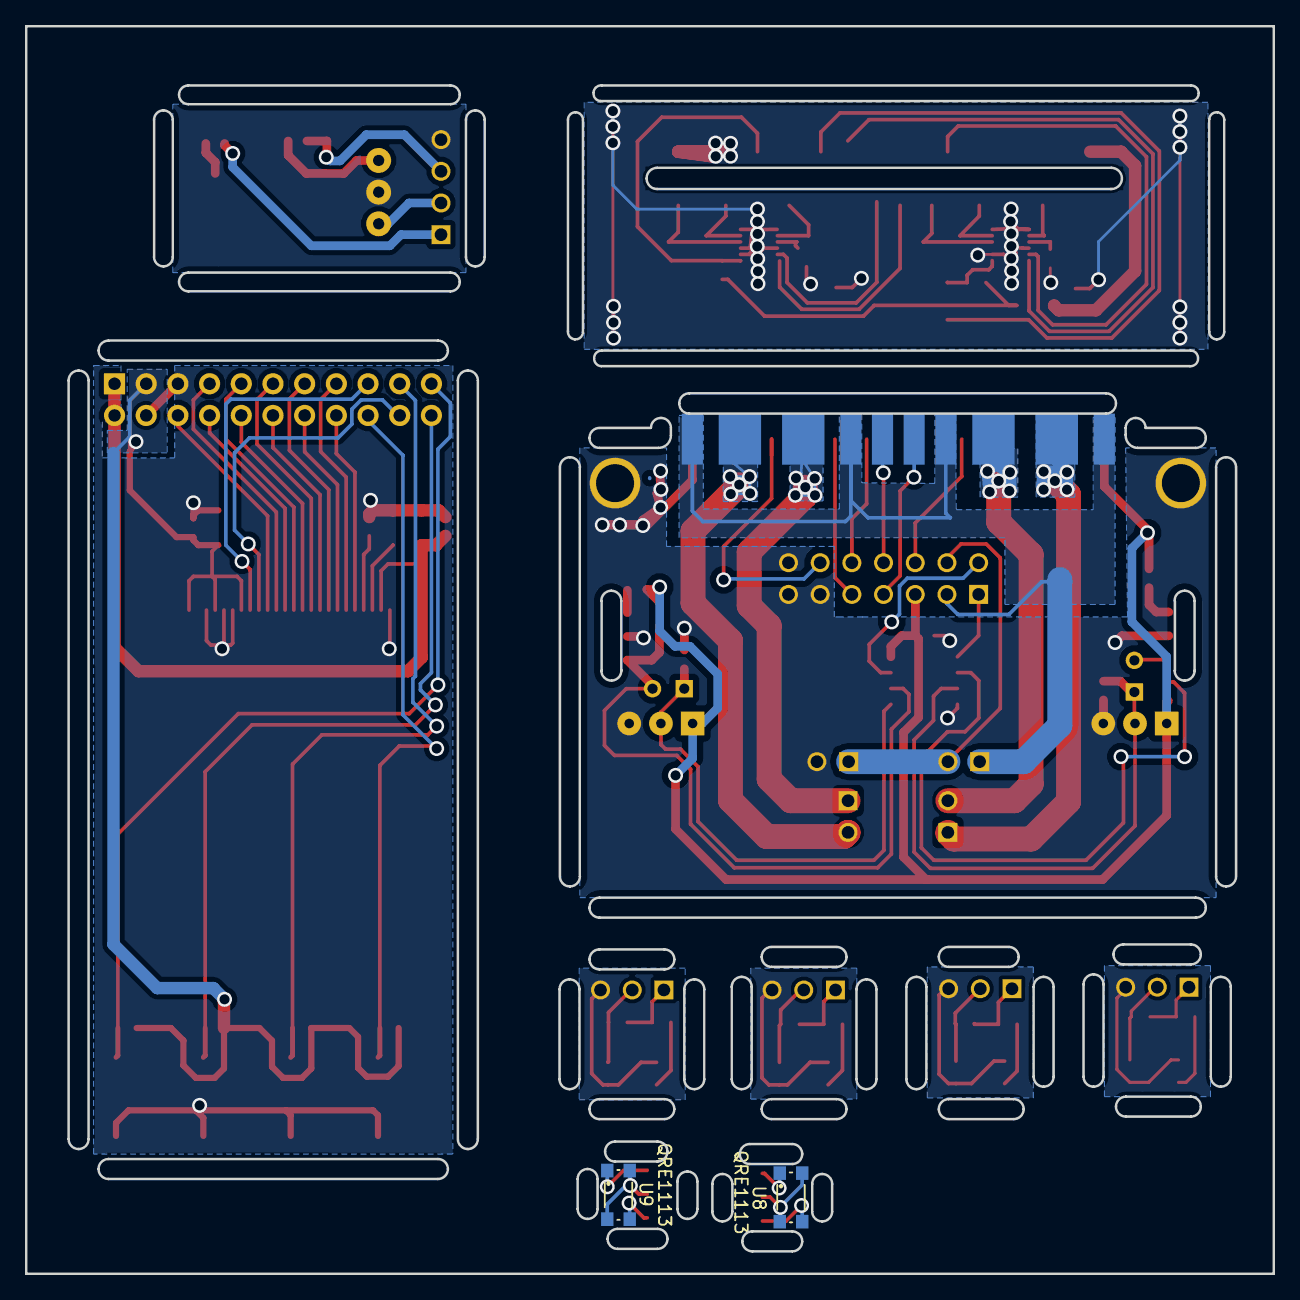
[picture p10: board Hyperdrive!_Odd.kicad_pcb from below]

Board: 2 copper layers, 100.0 x 100.0 mm, 70 parts (2 on the bottom side), 79 nets.

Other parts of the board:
JP1, JP2: Jump_2mm
TP1, TP2: SIL-2
VAL: REF; Hyperdrive!_F.SilkS_20mm

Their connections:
+3.3V: JP1.1, JP1.2; also elsewhere on the board
/FAULTR: JP2.1, JP2.2; also elsewhere on the board
unnamed 52: TP2.2; also elsewhere on the board
unnamed 54: TP1.2; also elsewhere on the board
unnamed 72: TP2.1; also elsewhere on the board
unnamed 73: TP1.1; also elsewhere on the board

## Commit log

2015-08-04 Added main project files
    [1200mAh_LiPoly.skp, 43.2x22_Wheel.skp, Gull_Wing.skp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]
2015-08-25 Updated 3D-Model, and finished main PCB
    [Display_PCB.kicad_pcb, Display_PCB.sch, Hyperdrive!.kicad_pcb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]
2015-08-28 Updated 3D-Model, and PCBs.
    [Display.skp, Display_PCB.skp, Header_11x2.skp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]
